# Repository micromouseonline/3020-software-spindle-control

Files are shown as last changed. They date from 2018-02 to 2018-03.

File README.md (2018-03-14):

# 3020 SOFTWARE SPINDLE CONTROL

Thanks to [Johnny](https://hackaday.io/Johnny) from [hackaday.io](http://hackaday.io) for his [fantastic work](https://hackaday.io/project/6776-3040-cnc-milling-machine-mods/log/21618-jp-1482-spindle-controller-schematic) reverse-engineering the JP-1481 spindle board, seen below:

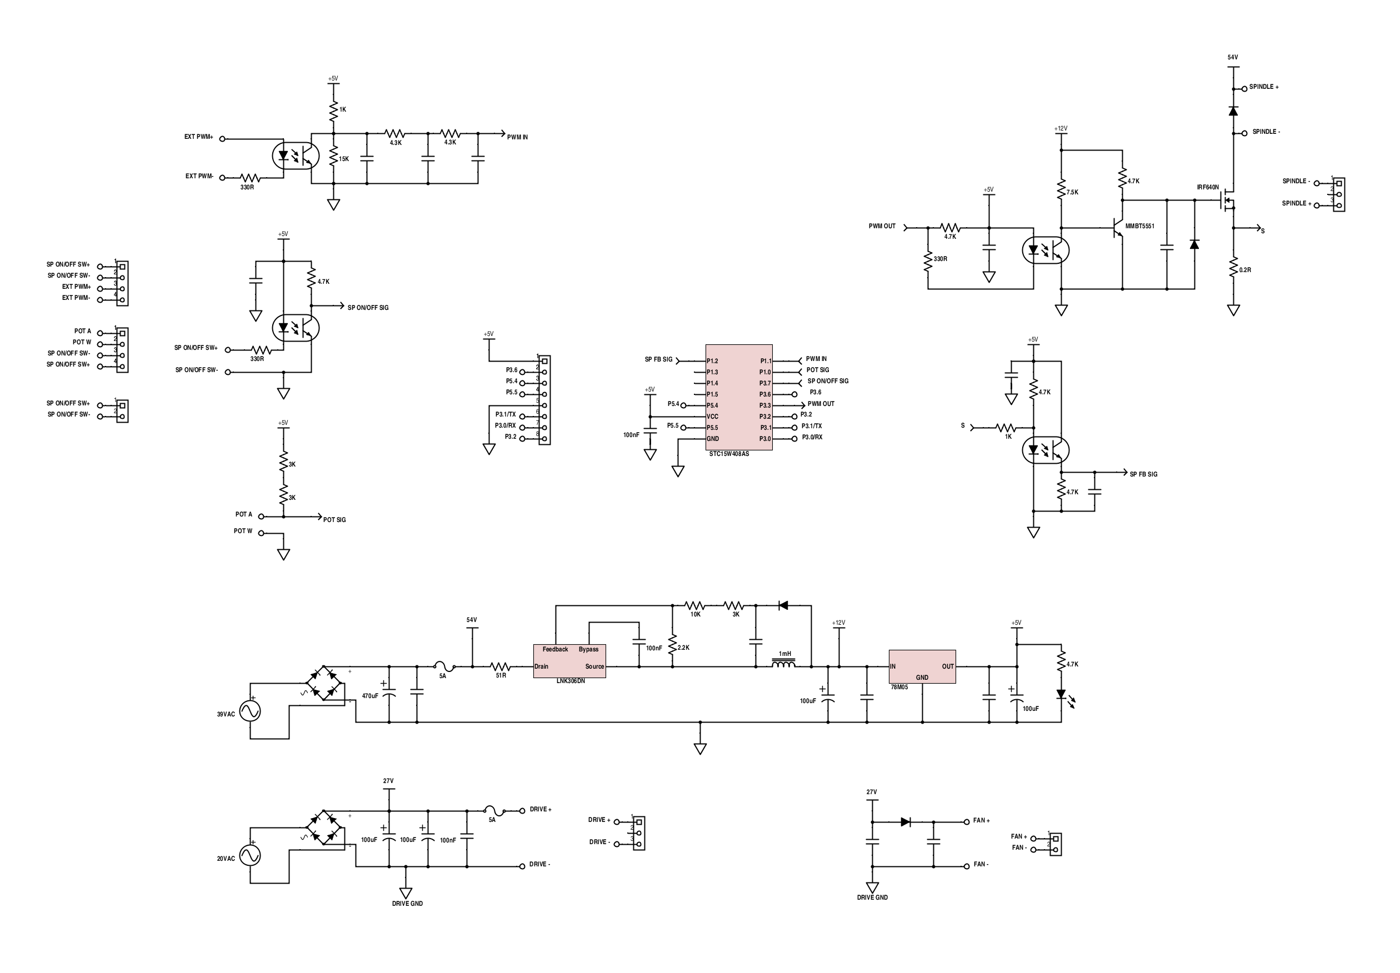
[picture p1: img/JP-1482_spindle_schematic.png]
JP-1482 Schematic


### Problem

**You cannot control the spindle speed by any means other than the front panel knob.**

This is particularly important in an emergency stop situation.  While your controller will the stepper movement, the spindle will continue to spin.

The main interface (JP-382C) board routes pin 17 of the parallel port directly to the (unpopulated) "PWM OUT" connector on that board.  

The JP-1482 (spindle control) board has a PWM input, but the firmware on the STC15W408AS (the MCU that ultimately controls spindle speed) _does not_ respond to that input.  

### Solution

The solution is to use another MCU that reads from the existing front-panel knob, and the PWM from the interface board, that then simulates the front panel knob (using a programmable potentiometer).

The goal is to have a board you can simply plug in, and it _just works_.™

### Implementation

For the sake of ease, and getting up-and-running quickly, I opted to use an Arduino Pro Micro (5V), which I happened to have on hand.

The input PWM is buffered through a 6N136 opto isolator (since the PWM power supply is floating), and fed directly into the Arudino.

For output, there is an MCP41010 digital potentiometer, controlled via SPI. Since the front panel pot is 5K, we're only going to use ½ of it's 10K range.

Power (5v) is provided by the PWM board.

The software is standard Arduino code, though I'm using PlatformIO CLI since I'm not a big fan the Arduino IDE.  Why not bare metal AVR? This isn't a demanding application, and while the Arduino ecosystem isn't the most efficient, it does make it quick and easy to get things up-and-running.

### Construction

##### Schematic

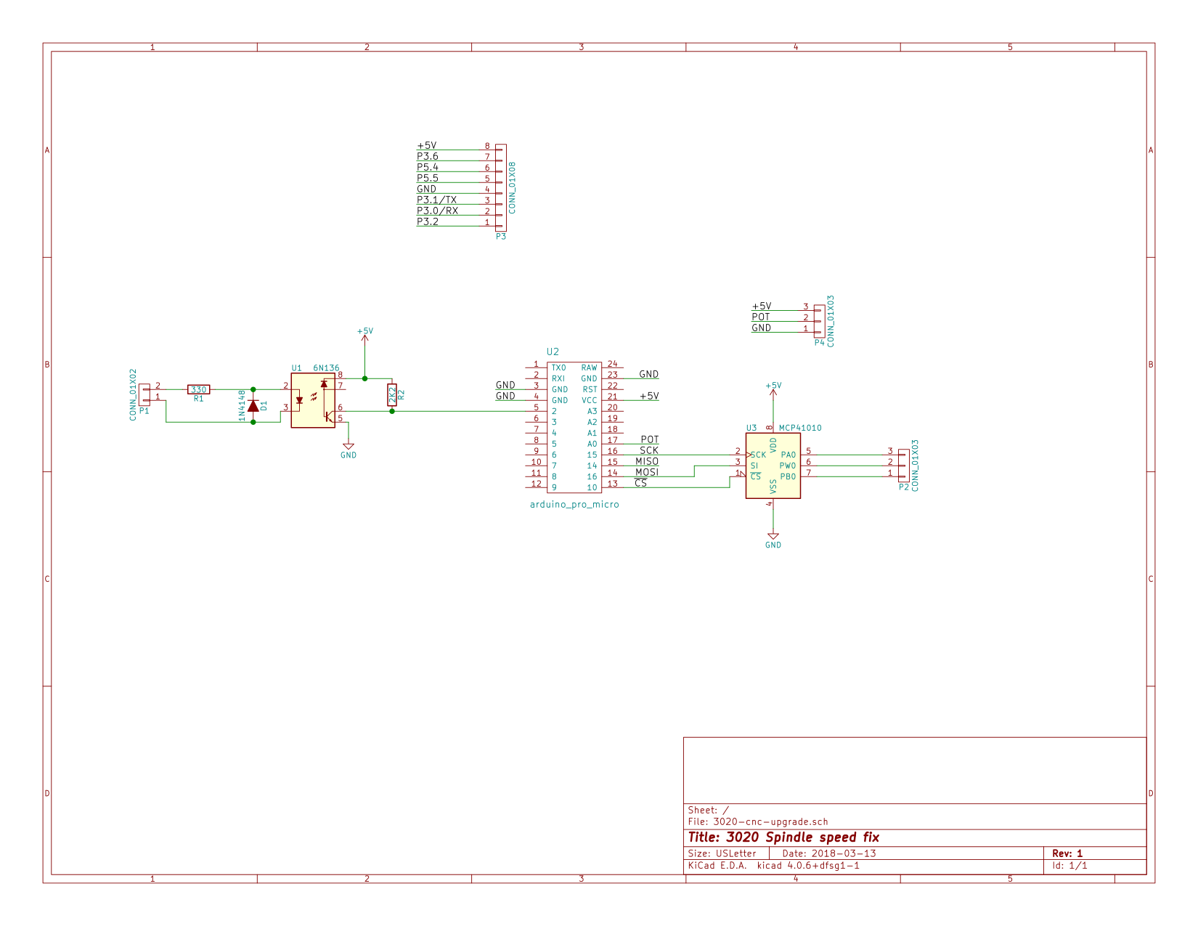
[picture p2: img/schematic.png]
Schematic


##### BOM

| Ref | P/N |
|---|---|
| P1 | B2B-XH-A(LF)(SN)|
| P2, P4| B3B-XH-A(LF)(SN) |
| P3 | B8B-XH-A(LF)(SN) |
| R1 | Any 0802 330 ohm SMT resistor|
| R2 | Any 0802 2200 ohm SMT resistor |
| D1 | 1N4148 (optional)|
| U1 | 6N136, 8 DIP |
| U2 | Arduino Pro Micro (Ebay clone) |
| U3 | MCP41010, 8 DIP |

The connectors on the board are compatible with the connectors on the JP-1482; they're the JST XH series. Be careful buying random "XH" connectors from Ebay or even Amazon, for two reasons:

1. The connectors are often 2.54mm pitch, instead of 2.50mm (XH is 2.50mm).  This will mostly work, but for the 8-pin connector, you're going to bend the pins of your board connector by doing this.
1. Make sure the cables you use are the "straight through" type -- pin 1 on one end goes to pin 1 on the other end.

Buy genuine XH connectors and cables from a reputable supplier (e.g. Digi-key).

The board layout is rather tight.  It's designed to have U1 and U3 soldered directly to the board, while U2 is in a socket, for ease of swapping, above the other ICs.

#### Compiling and installing firmware from source

###### Step 1:
[Install Platformio](http://docs.platformio.org/en/latest/installation.html)

###### Step 2

You may need to add the `--upload-port` parameter, depending on how your system enumerates the Arduino port.

```bash
cd 3020-software-spindle-control/fw
platformio run -t upload
```

#### Installing from pre-compiled `.hex` file

--- nothing here yet ---

#### Behavior

The code will measure the input PWM from your controller, and monitors the front panel spindle control knob.  The front panel knob sets the _maximum_ speed.  If this knob is at zero, the spindle will not be enabled.  Example: if the knob is at the 60% position, and you command a 30% spindle speed via PWM, then the output speed will be 18% (0.3 x 0.6) of spindle absolute maximum speed. Also, the spindle on/off switch overrides everything else when in the off position.

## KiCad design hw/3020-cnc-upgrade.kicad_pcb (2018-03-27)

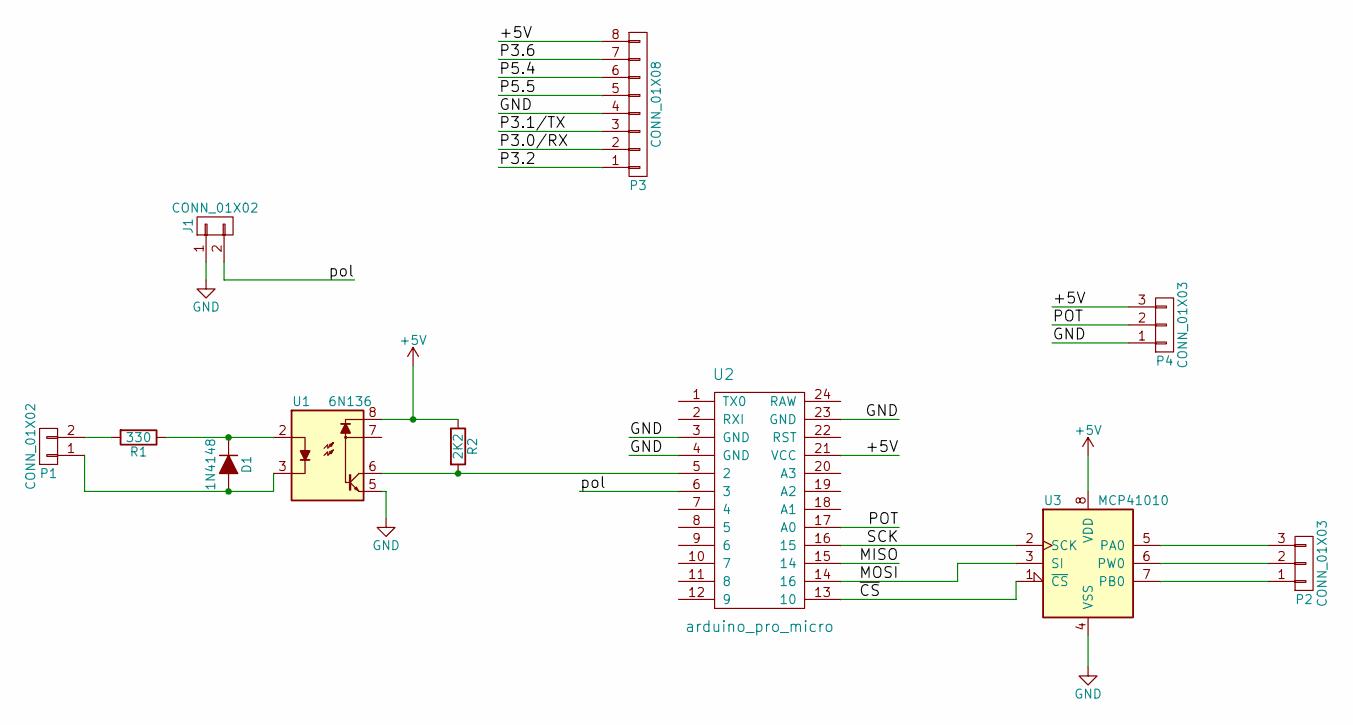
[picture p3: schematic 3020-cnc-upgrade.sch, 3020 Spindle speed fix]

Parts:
D1: 1N4148; SOD-123
J1: CONN_01X02; Pin_Header_Straight_1x02_Pitch2.54mm
P1: CONN_01X02; JST_XH_B02B-XH-A_02x2.50mm_Straight
P2, P4: CONN_01X03; JST_XH_B03B-XH-A_03x2.50mm_Straight
P3: CONN_01X08; JST_XH_B08B-XH-A_08x2.50mm_Straight
R1: 330; R_0805
R2: 2K2; R_0805
U1: 6N136; DIP-8_W7.62mm
U2: arduino_pro_micro; DIP-24_W15.24mm
U3: MCP41010; DIP-8_W7.62mm

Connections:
+5V: P3.8, P4.3, R2.1, U1.8, U2.21 (VCC), U3.8 (VDD)
/MISO: U2.15 (14)
/MOSI: U2.14 (16), U3.3 (SI)
/P3.0/RX: P3.2
/P3.1/TX: P3.3
/P3.2: P3.1
/P3.6: P3.7
/P5.4: P3.6
/P5.5: P3.5
/POT: P4.2, U2.17 (A0)
/SCK: U2.16 (15), U3.2 (SCK)
/pol: J1.2, U2.6 (3)
/~CS: U2.13 (10), U3.1 (~CS)
GND: J1.1, P3.4, P4.1, U1.5, U2.3 (GND), U2.4 (GND), U2.23 (GND), U3.4 (VSS)
unnamed: D1.1 (K), R1.1, U1.2
unnamed: D1.2 (A), P1.1, U1.3
unnamed: P1.2, R1.2
unnamed: P2.1, U3.7 (PB0)
unnamed: P2.2, U3.6 (PW0)
unnamed: P2.3, U3.5 (PA0)
unnamed: R2.2, U1.6, U2.5 (2)

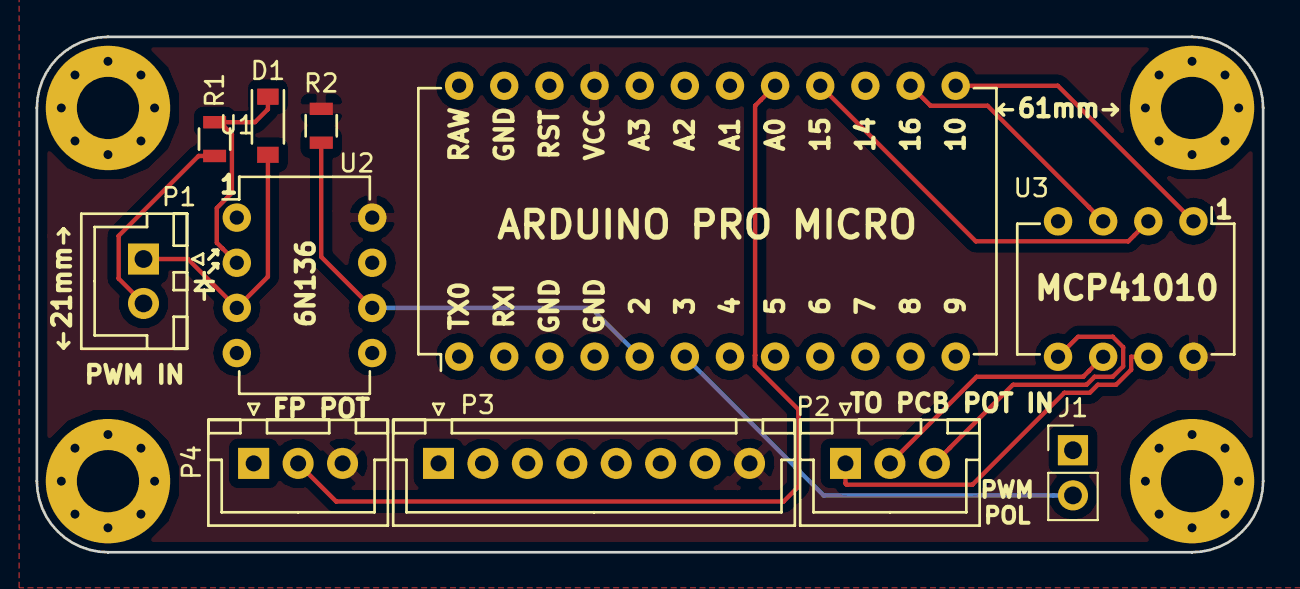
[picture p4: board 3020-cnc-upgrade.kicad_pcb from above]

Board: 2 copper layers, 69.0 x 29.0 mm, 11 parts (0 on the bottom side), 14 nets.

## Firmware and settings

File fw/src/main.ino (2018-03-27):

#include <elapsedMillis.h>
#include <SPI.h>

#define PWM_IN_PIN 2
#define POL_PIN 3
#define POT_IN_PIN 0
#define CS_PIN 10
#define SCK_PIN 15
#define MOSI_PIN 16
#define AVG_LEN 15
#define LED_PIN 17

#define MAX(x,y) (x) > (y) ? (x) : (y)
#define MIN(x,y) (x) < (y) ? (x) : (y)

//#define DEBUG

SPISettings spiSet(5000000, MSBFIRST, SPI_MODE0);

volatile int onTime = 0;
volatile int offTime = 0;
volatile long lastTime = 0;
elapsedMillis outputTimer;
elapsedMillis printTimer;
elapsedMillis ledTimer;
uint16_t ledState = 200;

volatile bool invertPolarity;

float pwmPcts[AVG_LEN];
float outputPct;
float pwmPct;
float potPct;

void interrupt () {
    long now = micros();
    long elapsed = lastTime - now;
    bool state = digitalRead(PWM_IN_PIN) ^ invertPolarity; 

    // this is backwards because the opto inverts
    if (state) { 
        offTime = elapsed;
    } else {
        onTime = elapsed;
    }

    lastTime = now;
}

void setup() {

    pinMode(PWM_IN_PIN, INPUT_PULLUP);
    pinMode(POT_IN_PIN, INPUT);
    pinMode(CS_PIN, OUTPUT);
    pinMode(POL_PIN, INPUT_PULLUP);
    pinMode(LED_PIN, OUTPUT);
    digitalWrite(LED_PIN, HIGH);

    SPI.begin();
    setOutput(0);

    attachInterrupt(digitalPinToInterrupt(PWM_IN_PIN), interrupt, CHANGE);
    Serial.begin(115200);

    for (int i = 0; i < AVG_LEN; ++i) {
        pwmPcts[i] = 0;
    }

    pwmPct = 0;
    potPct = 0;
    outputPct = 0;
}

void setOutput(float pct) {


    // We're emulating a 5K pot with a
    // 10K digi-pot, so we're
    // only going to use 1/2 the range

    uint8_t value = 0x80 + pct * 0x7f;
    SPI.beginTransaction(spiSet);
    digitalWrite(CS_PIN, LOW);
    SPI.transfer(0x11); // Write potentiometer 0
    SPI.transfer(value); // Set wiper position
    digitalWrite(CS_PIN, HIGH);
    SPI.endTransaction();
}

void setLedPct(float pct) {
    if (pct <=0) {
        ledState = 0;
    } else if (pct >= 1) {
        ledState = 1;
    } else {
        ledState = (1.0 - pct) * 1000;
    }
}

void loop() {

    static int pctIndex = 0;
    invertPolarity = digitalRead(POL_PIN);

    float cur = digitalRead(PWM_IN_PIN);
    cur = invertPolarity ? 1.0 - cur : cur;

    noInterrupts();
    // copy values out fast.
    long l = lastTime;
    int o = onTime;
    int f = offTime;
    interrupts();

    // BEGIN
    //
    // If we put this code in the 
    // "nointerrupts" block above, 
    // then narrow PWM times become
    // unstable
    long now = micros();
    long elapsed = now - l;
    if (elapsed < 100000) { // 100ms
        cur = (float)o / (float)(o + f);
    } 
    // END


    if (ledState < 2) {
        digitalWrite(LED_PIN, !ledState);
        ledTimer = 0;
    } else if (ledTimer > ledState) {
        digitalWrite(LED_PIN, !digitalRead(LED_PIN));
        ledTimer = 0;
    }

    pwmPcts[pctIndex++] = cur;

    if (pctIndex >= AVG_LEN) {
        pctIndex = 0;
    }

    if (outputTimer > 10) {
        pwmPct = 0;

        for (int i = 0; i < AVG_LEN; ++i) {
            pwmPct += pwmPcts[i];
        }

        pwmPct /= AVG_LEN;
        potPct = analogRead(POT_IN_PIN) / 1023.0f;
        outputPct = pwmPct * potPct;

        setLedPct(outputPct);
        setOutput(outputPct);
        outputTimer = 0;
    }

#ifdef DEBUG
    if (printTimer > 75) {
        Serial.print("PWM in: ");
        Serial.print(pwmPct*100);
        Serial.print("%");
        Serial.print(" POT in: ");
        Serial.print(potPct*100);
        Serial.print("  out: ");
        Serial.print(outputPct * 100);
        Serial.println();
        printTimer = 0;
    }
#endif
}

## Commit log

2018-02-01 pcb and schem initial commit
    [3020-cnc-upgrade.kicad_pcb, 3020-cnc-upgrade.sch]
2018-02-10 pcb layout
    [3020-cnc-upgrade.kicad_pcb, 3020-cnc-upgrade.sch]
2018-02-10 updates to layout
    [3020-cnc-upgrade.kicad_pcb]
2018-02-13 minor updates to hw
    [3020-cnc-upgrade.kicad_pcb, 3020-cnc-upgrade.sch]
2018-02-21 hardware updates
    [3020-cnc-upgrade.kicad_pcb, 3020-cnc-upgrade.sch]
2018-03-07 swapped pins on pwm input
    [3020-cnc-upgrade.kicad_pcb, 3020-cnc-upgrade.sch]
2018-03-13 updates to board and schematic
    [3020-cnc-upgrade.sch]
2018-03-13 added URL and revision to board
    [3020-cnc-upgrade.kicad_pcb, 3020-cnc-upgrade.sch]
2018-03-14 added schematic image
2018-03-14 minor PCB tweak
    [3020-cnc-upgrade.kicad_pcb]
2018-03-26 made debug printing optional
2018-03-27 added jumper to reverse spindle polarity
    [3020-cnc-upgrade.kicad_pcb, 3020-cnc-upgrade.sch, _saved_3020-cnc-upgrade.sch]
2018-03-27 added LED for debugging, and polarity inversion
